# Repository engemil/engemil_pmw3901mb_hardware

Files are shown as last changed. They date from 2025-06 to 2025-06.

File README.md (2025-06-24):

# EngEmil PMW3901MB Optical Flow Sensor Module

The EngEmil PMW3901MB Module is a Optical Motion Tracking Chip module, for optical position control of drones. The PCB module is designed with KiCAD 9.

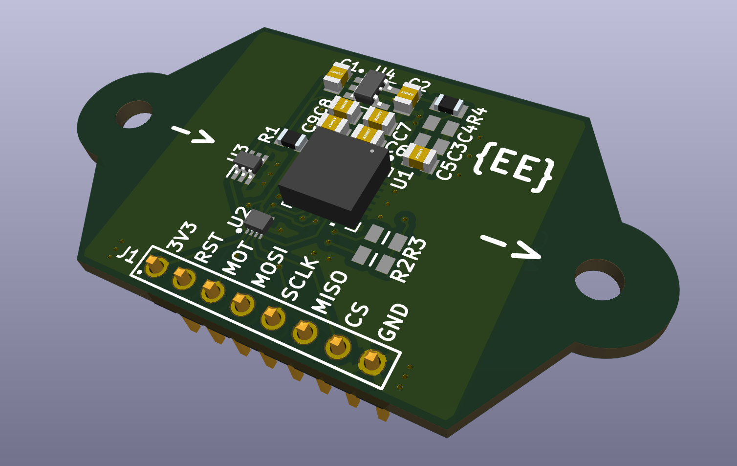
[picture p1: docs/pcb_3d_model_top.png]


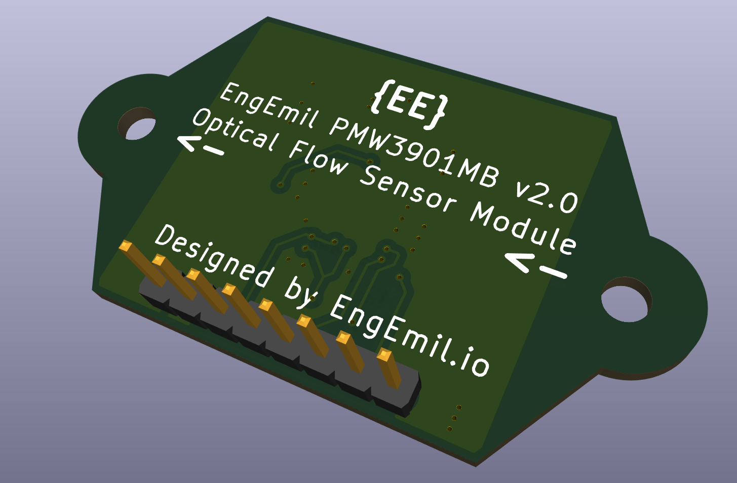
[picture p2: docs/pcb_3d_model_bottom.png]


## Versions

**Version 2**
- Removed 3v3 regulator and changed VCC pin text to 3V3
- Added ESD protection
- Added reverse voltage protection
- Added pull-up resistors for SCLK and MISO. Marked as not mounted.
- Added resistor for RC-filter for PMW3901MB. Marked as R4=0ohm, and C3 and C4 not mounted. Note added in schematic.

**Version 1**
- First prototype
- 3v3 regulator and 1v8 regulator
- Standard pins
- 2 mounting holes

## Links

- PMW3901MB-TXQT https://www.pixart.com/products-detail/44/PMW3901MB-TXQT
- Generating Gerbers (Manufacturer Recommendations): https://docs.oshpark.com/design-tools/kicad/generating-kicad-gerbers/
- Design Rule (Manufacturer Recommendations):
    - https://docs.oshpark.com/design-tools/kicad/kicad-design-rules/
    - https://www.pcbway.com/pcb_prototype/Pinted_Circuit_Board_Prototype.html
    - https://www.pcbway.com/capabilities.html
    - https://jlcpcb.com/capabilities/pcb-capabilities

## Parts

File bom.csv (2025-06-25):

Item # | Quantity | Manufacturer Part # | Description | Reference Designators | Not mount | Mounting Type | Package/Footprint | Manufacturer | Manufacturer Part Page | Note | Vendor #1 | Vendor #2 | Vendor #3
1 | 1 | TLV77318PDBVR | Fixed 1.8V voltage regulator | U4 |  | SMD | SOT-23-5 (DBV) | Texas Instrument | https://www.ti.com/product/TLV773/part-details/TLV77318PDBVR |  | https://www.digikey.no/no/products/detail/texas-instruments/tlv77318pdbvr/23331424 | https://no.mouser.com/ProductDetail/Texas-Instruments/TLV77318PDBVR?qs=i8QVZAFTkqTJuDP4u6TAYQ%3D%3D | https://lcsc.com/product-detail/Voltage-Regulators-Linear-Low-Drop-Out-LDO-Regulators_Texas-Instruments-TLV77318PDBVR_C32339535.html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
2 | 1 | 61300811121 | 2.54mm pitch 8 pins male through-hole headers | J1 |  | Through-hole |  | Würth Elektronik |  |  | https://www.digikey.no/en/products/detail/w%C3%BCrth-elektronik/61300811121/4846839
3 | 1 | PMW3901MB-TXQT | Optical Motion Tracing Chip | U1 |  | SMD | 28-pin QFN | Pixart | https://www.pixart.com/products-detail/44/PMW3901MB-TXQT |  | (Alibaba)
4 | 1 | RC0805FR-100RL | 0 Ohm 125mW resistor | R4 |  | SMD | 0805 in | YAGEO |  |  | https://no.mouser.com/ProductDetail/YAGEO/RC0805FR-100RL?qs=sGAEpiMZZMvdGkrng054t8AJgcdMkx7xHWXHpsqRQHI%3D
5 | 3 | RE0805FRE0710KL | 10k Ohm resistor | R1,R2,R3 | R2,R3 | SMD | 0805 in | YAGEO |  |  | https://no.mouser.com/ProductDetail/YAGEO/RE0805FRE0710KL
6 | 2 | C0805C226M9PAC7210 | 22uF ceramic non-polarity capacitor | C3,C4 | C3,C4 | SMD | 0805 in | YAGEO KEMET |  |  | https://no.mouser.com/ProductDetail/KEMET/C0805C226M9PAC7210?qs=kSrfU%2F8XGbk4aYGfk4dTXw%3D%3D
7 | 3 | C0805C104JMRECAUTO7210 | 100n/0.1uF ceramic non-polarity capacitor | C5,C6,C8 |  | SMD | 0805 in | YAGEO KEMET |  |  | https://no.mouser.com/ProductDetail/KEMET/C0805C104JMRECAUTO7210?qs=55YtniHzbhCWsM9aesOnTg%3D%3D
8 | 2 | C0805C105J4RECAUTO7210 | 1uF 16VDC 5% ceramic non-polarity capacitor | C1,C2 |  | SMD | 0805 in | YAGEO KEMET |  |  | https://no.mouser.com/ProductDetail/KEMET/C0805C105J4RECAUTO7210?qs=55YtniHzbhDbyzfJO59W6Q%3D%3D#
9 | 1 | C0805C106K4PAC7210 | 10uF ceramic non-polarity capacitor | C7 |  | SMD | 0805 in | YAGEO KEMET |  |  | https://no.mouser.com/ProductDetail/KEMET/C0805C106K4PAC7210?qs=zDkSFN9STR9jrJZBgSwCDA%3D%3D
10 | 1 | C0805C475K4RACAUTO7210 | 4.7uF ceramic non-polarity capacitor | C9 |  | SMD | 0805 in | YAGEO KEMET |  |  | https://no.mouser.com/ProductDetail/KEMET/C0805C475K4RACAUTO7210?qs=HXFqYaX1Q2xkgxFv524wgg%3D%3D
11 | 1 | TPD8E003DQDR | TVS diodes package | U2 |  | SMD |  | Texas Instrument |  |  | https://no.mouser.com/ProductDetail/Texas-Instruments/TPD8E003DQDR?qs=hEBn5lgDlCo1%252BvgoUxxo%252Bg%3D%3D
12 | 1 | LM66100QDCKRQ1 | Reverse polarity protection | U3 |  | SMD | SC70-6 | Texas Instrument | https://www.ti.com/product/LM66100-Q1 |  | https://no.mouser.com/ProductDetail/Texas-Instruments/LM66100QDCKRQ1?qs=MyNHzdoqoQIvjdvtKQd0jA%3D%3D

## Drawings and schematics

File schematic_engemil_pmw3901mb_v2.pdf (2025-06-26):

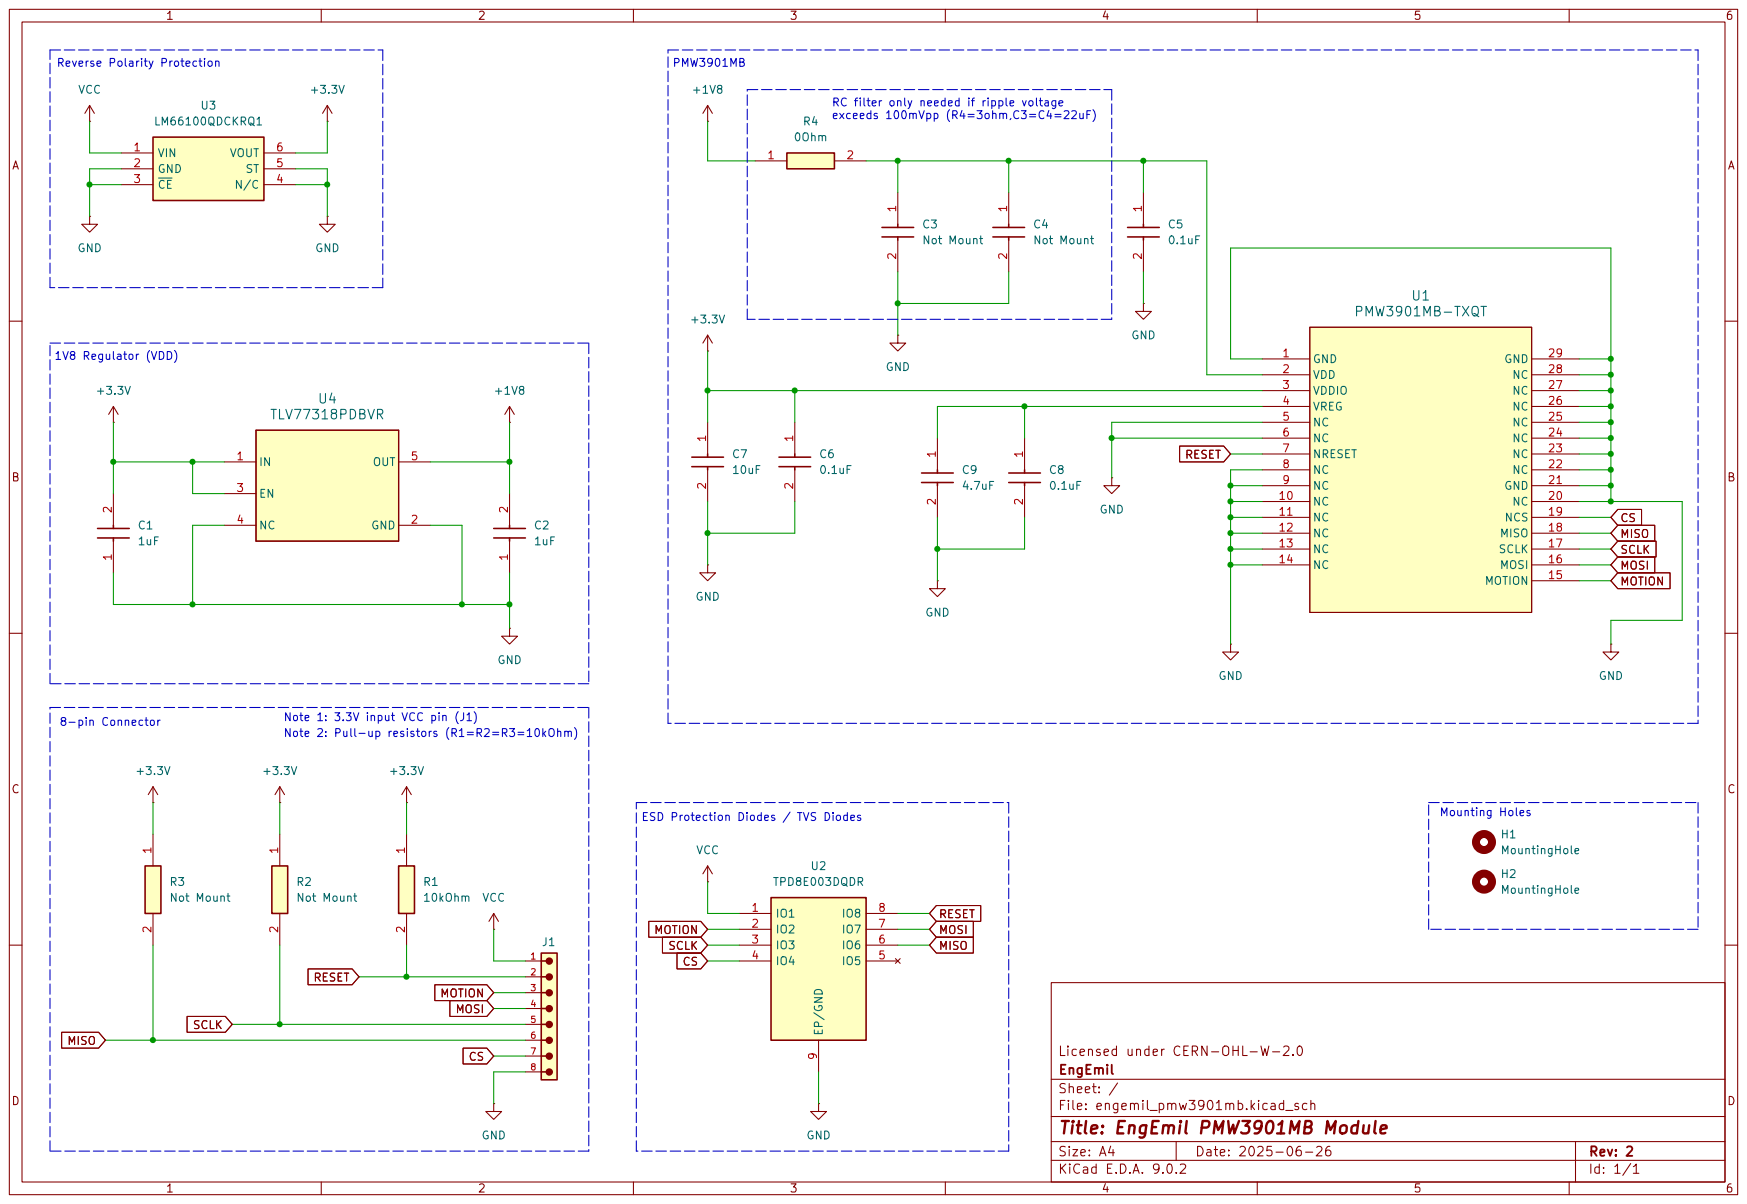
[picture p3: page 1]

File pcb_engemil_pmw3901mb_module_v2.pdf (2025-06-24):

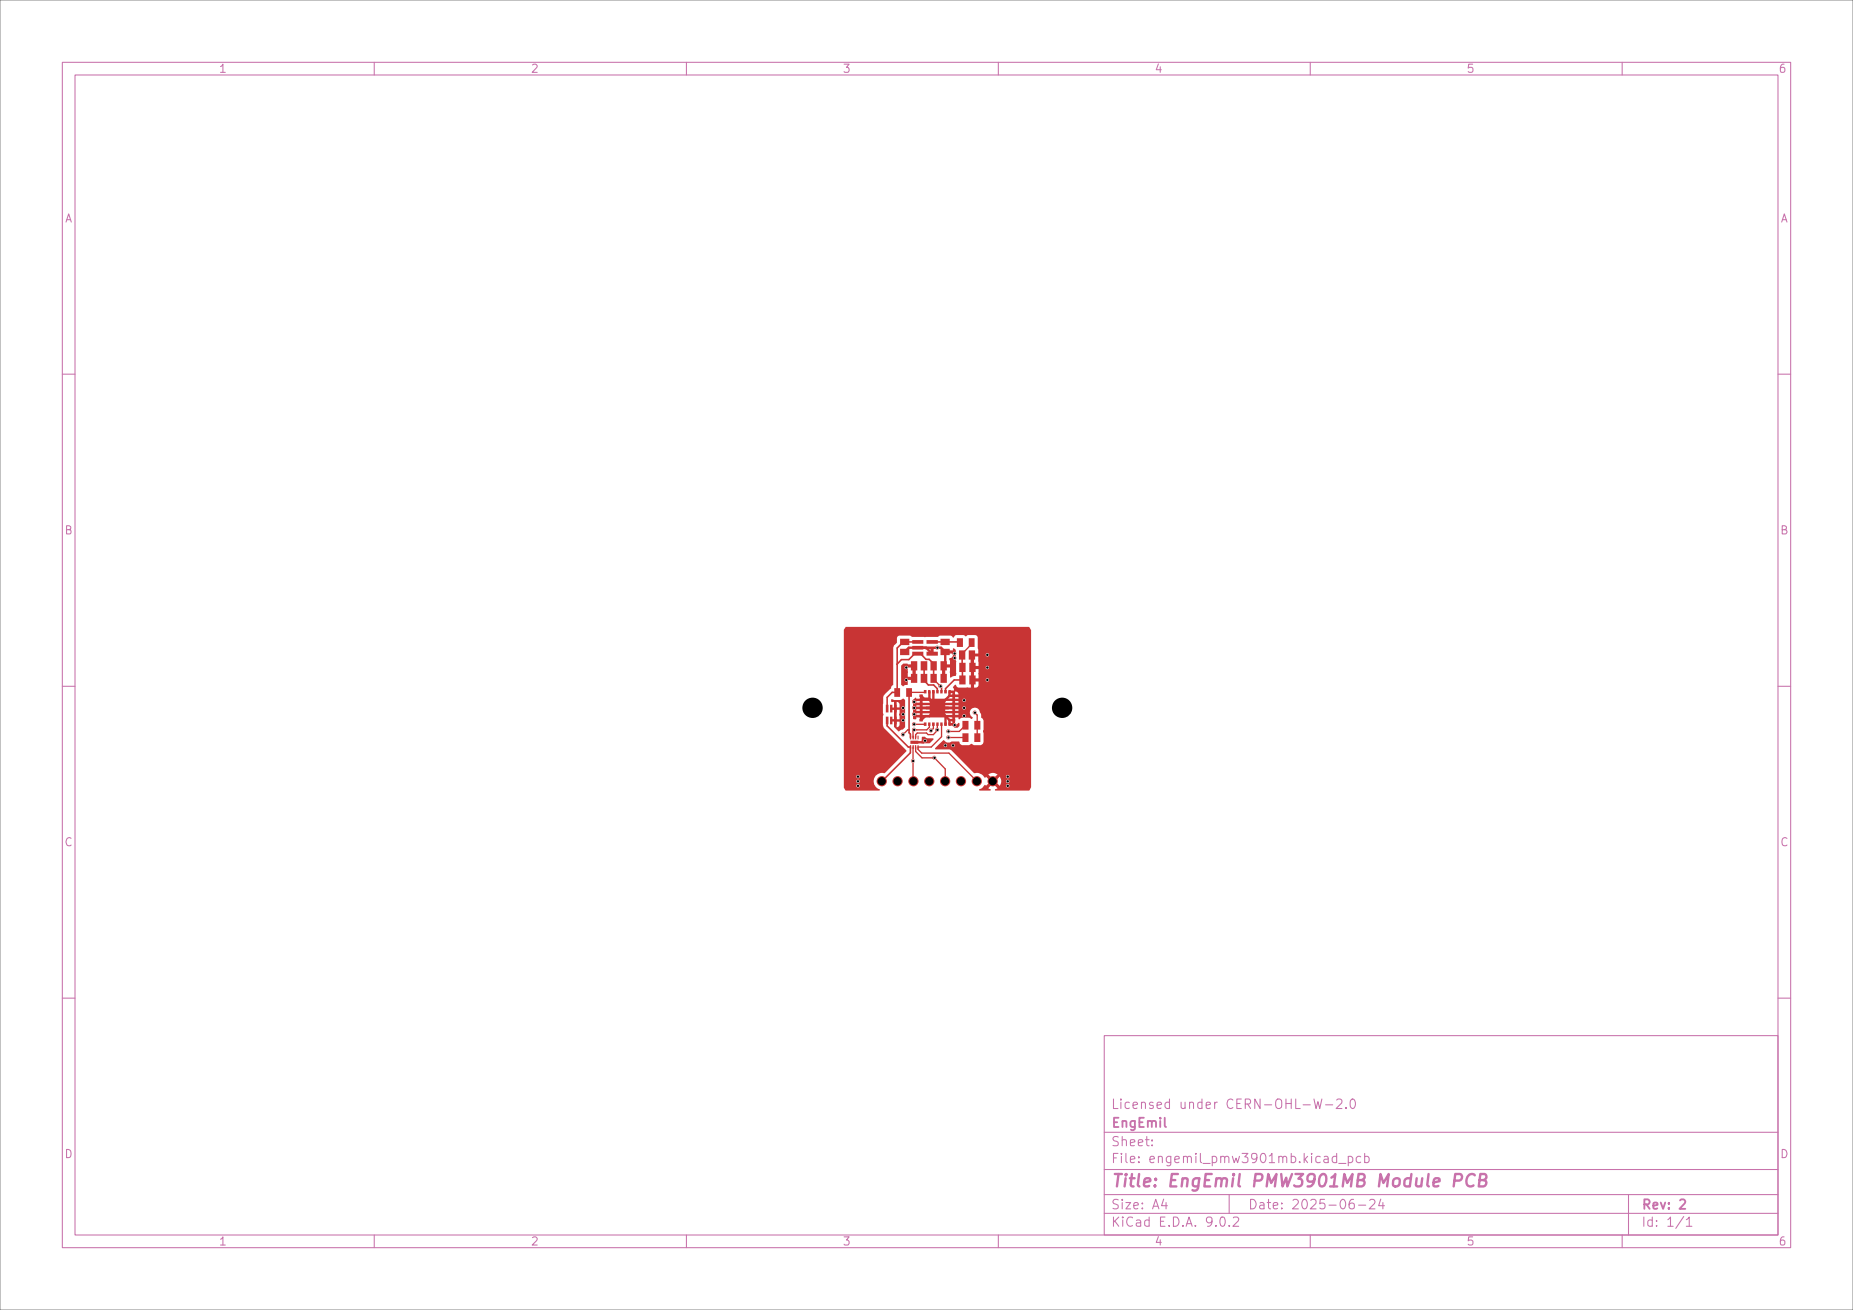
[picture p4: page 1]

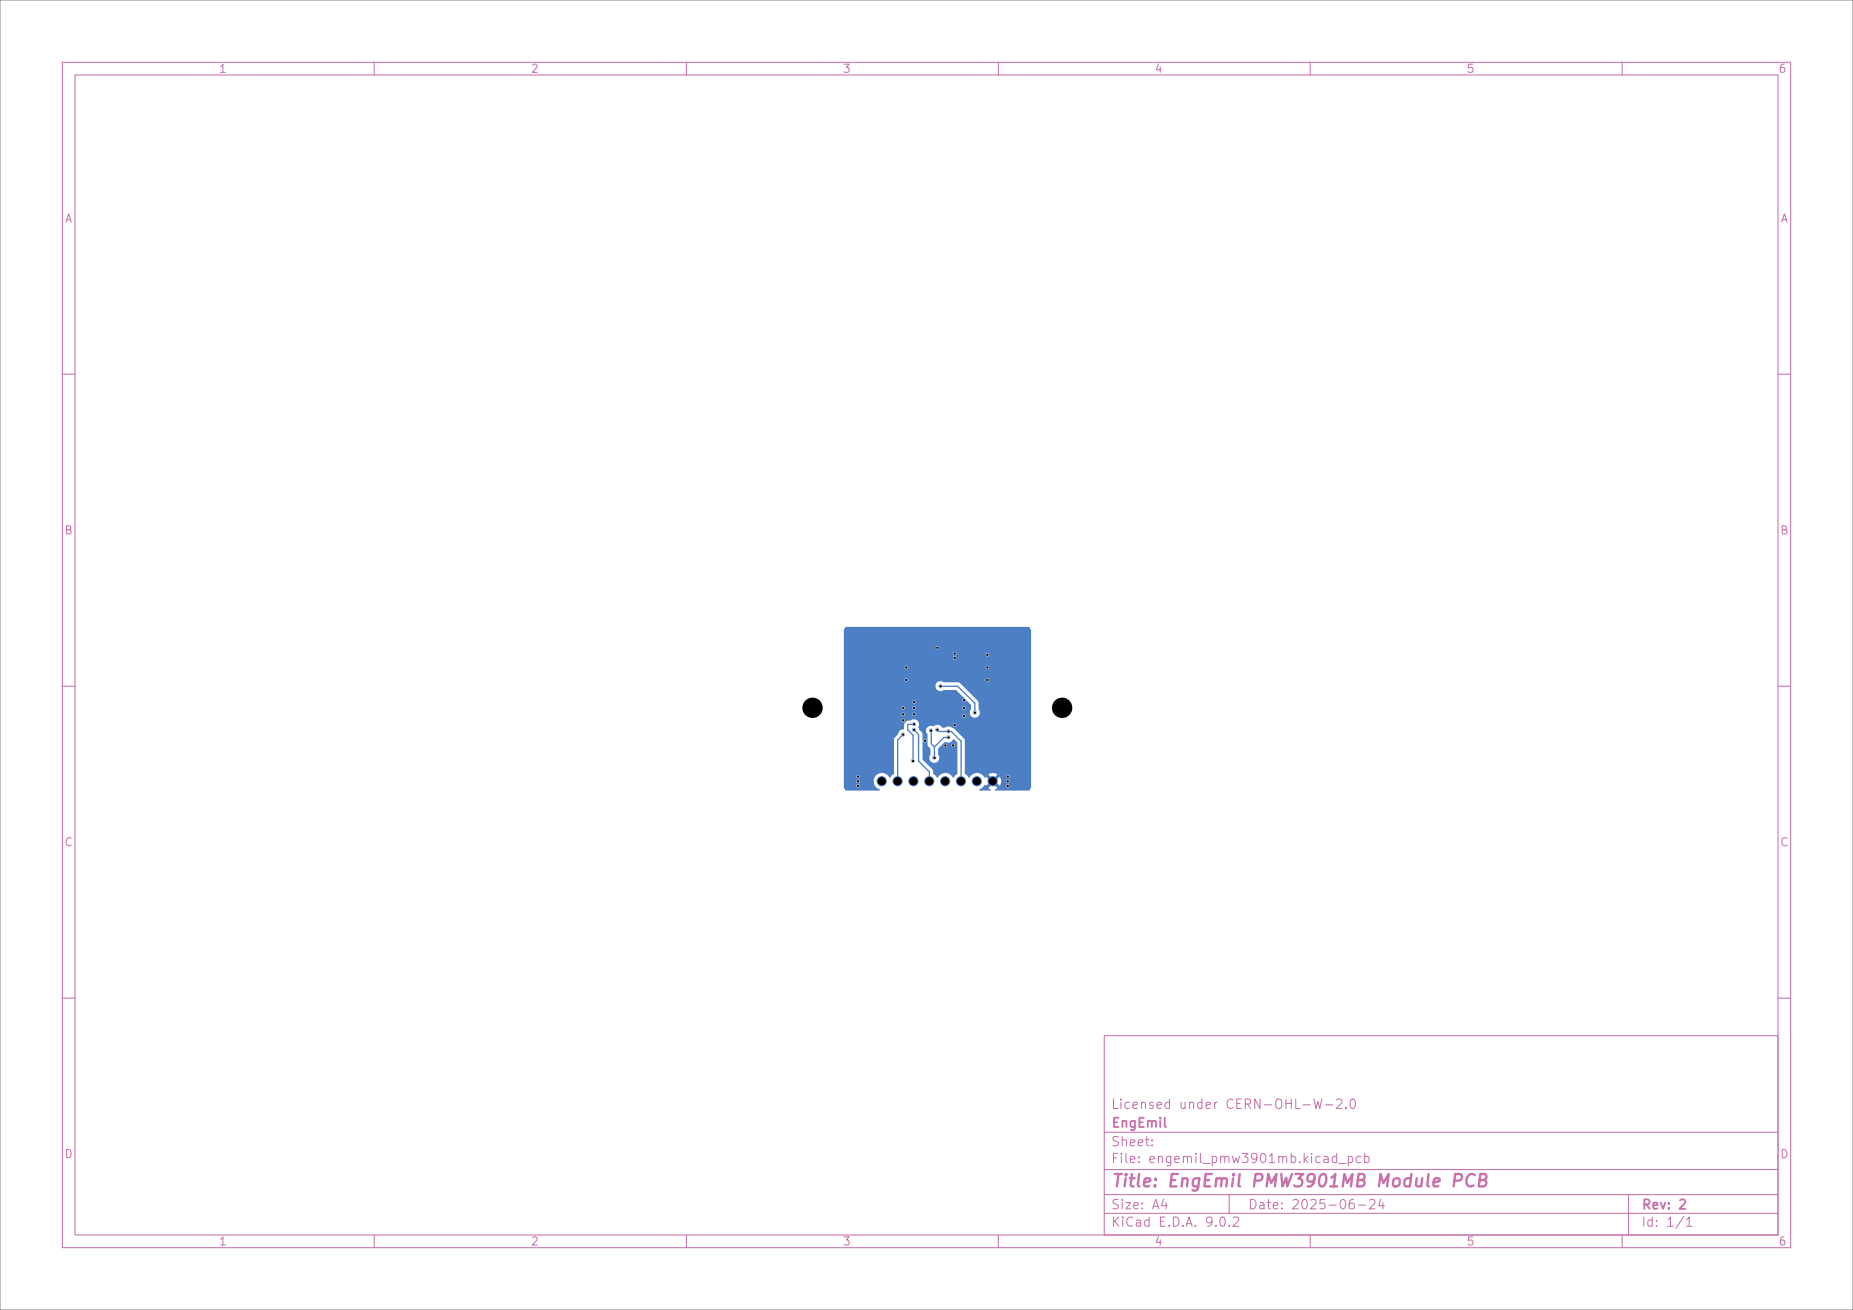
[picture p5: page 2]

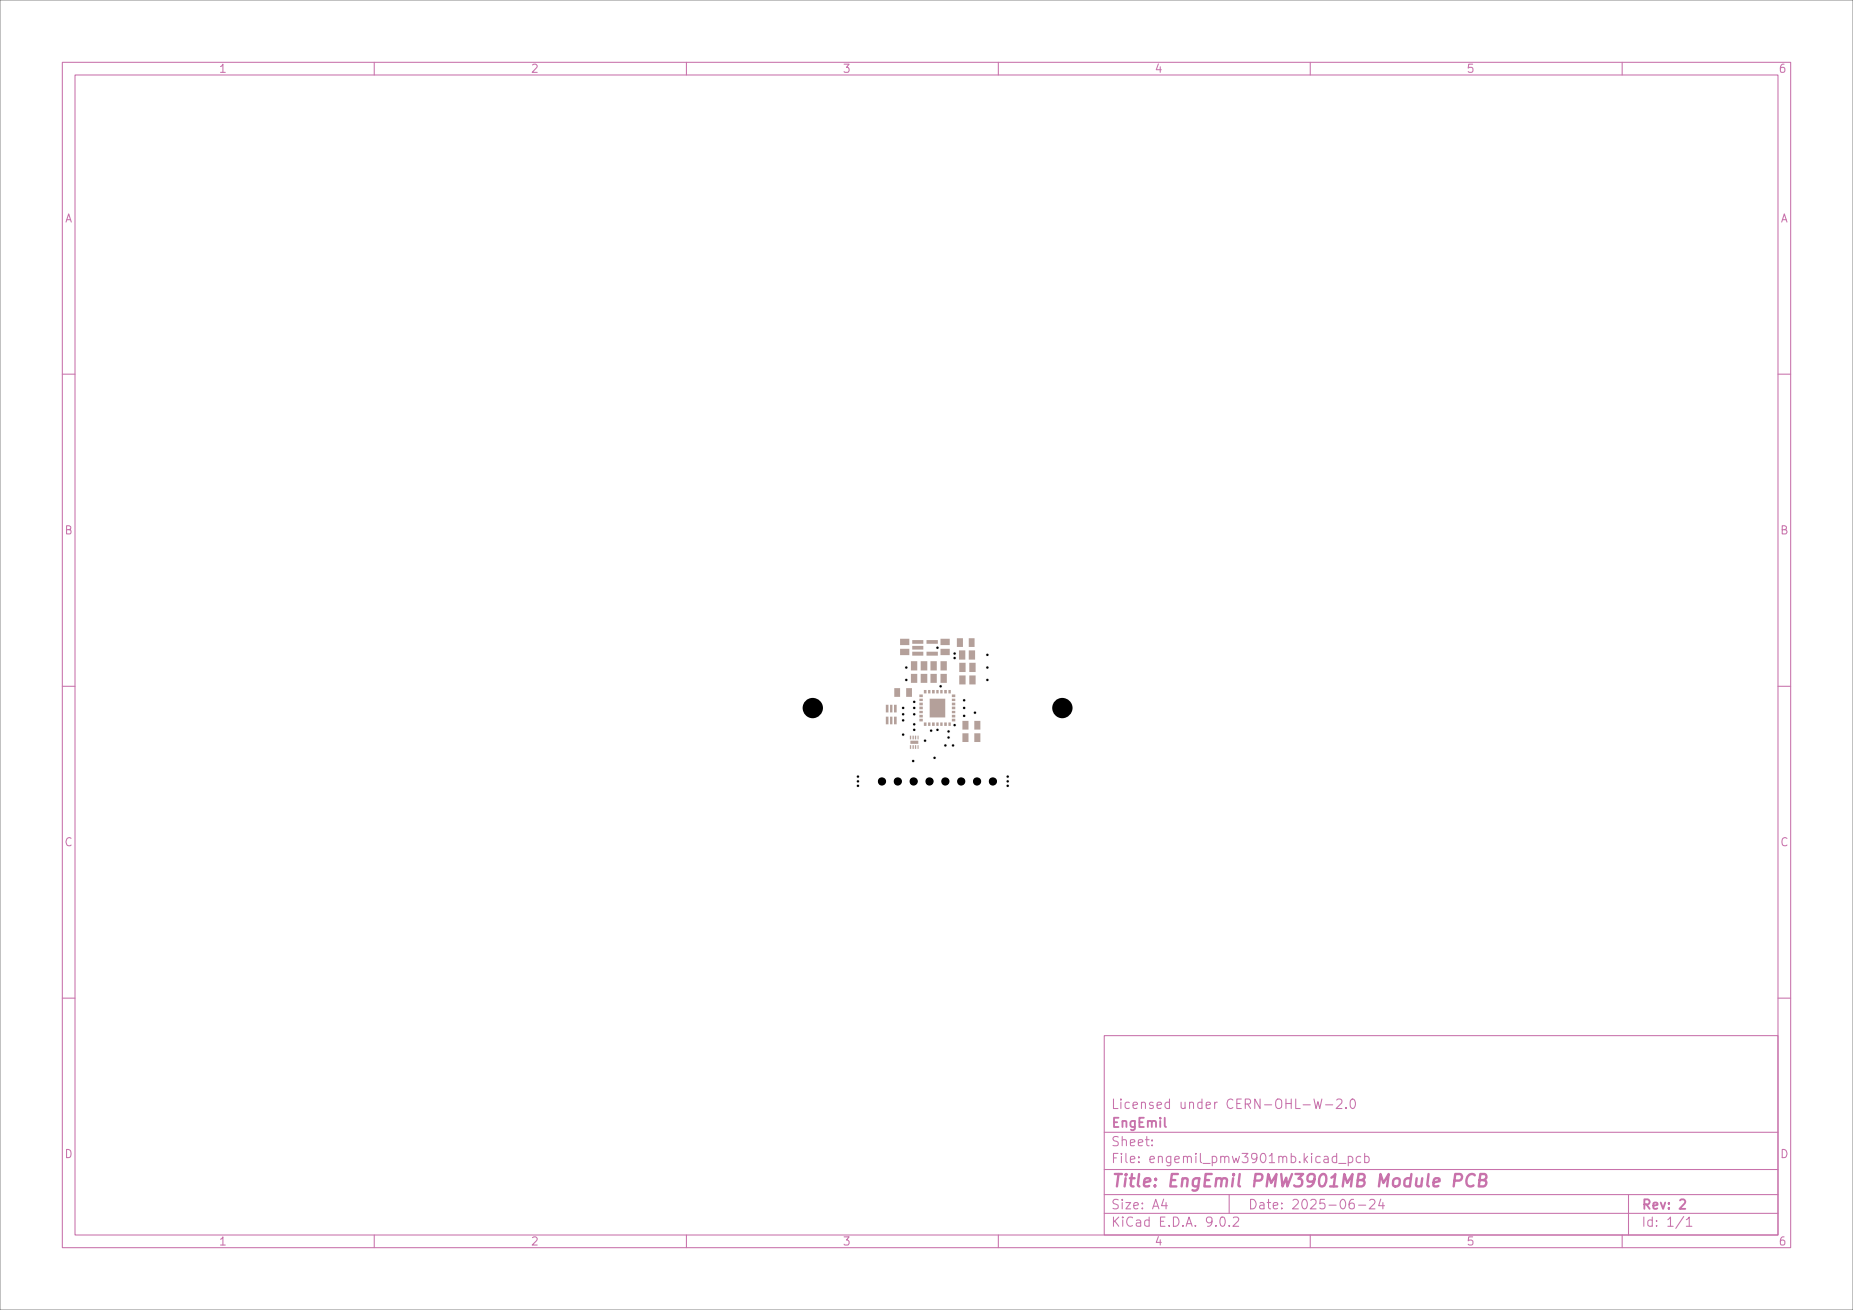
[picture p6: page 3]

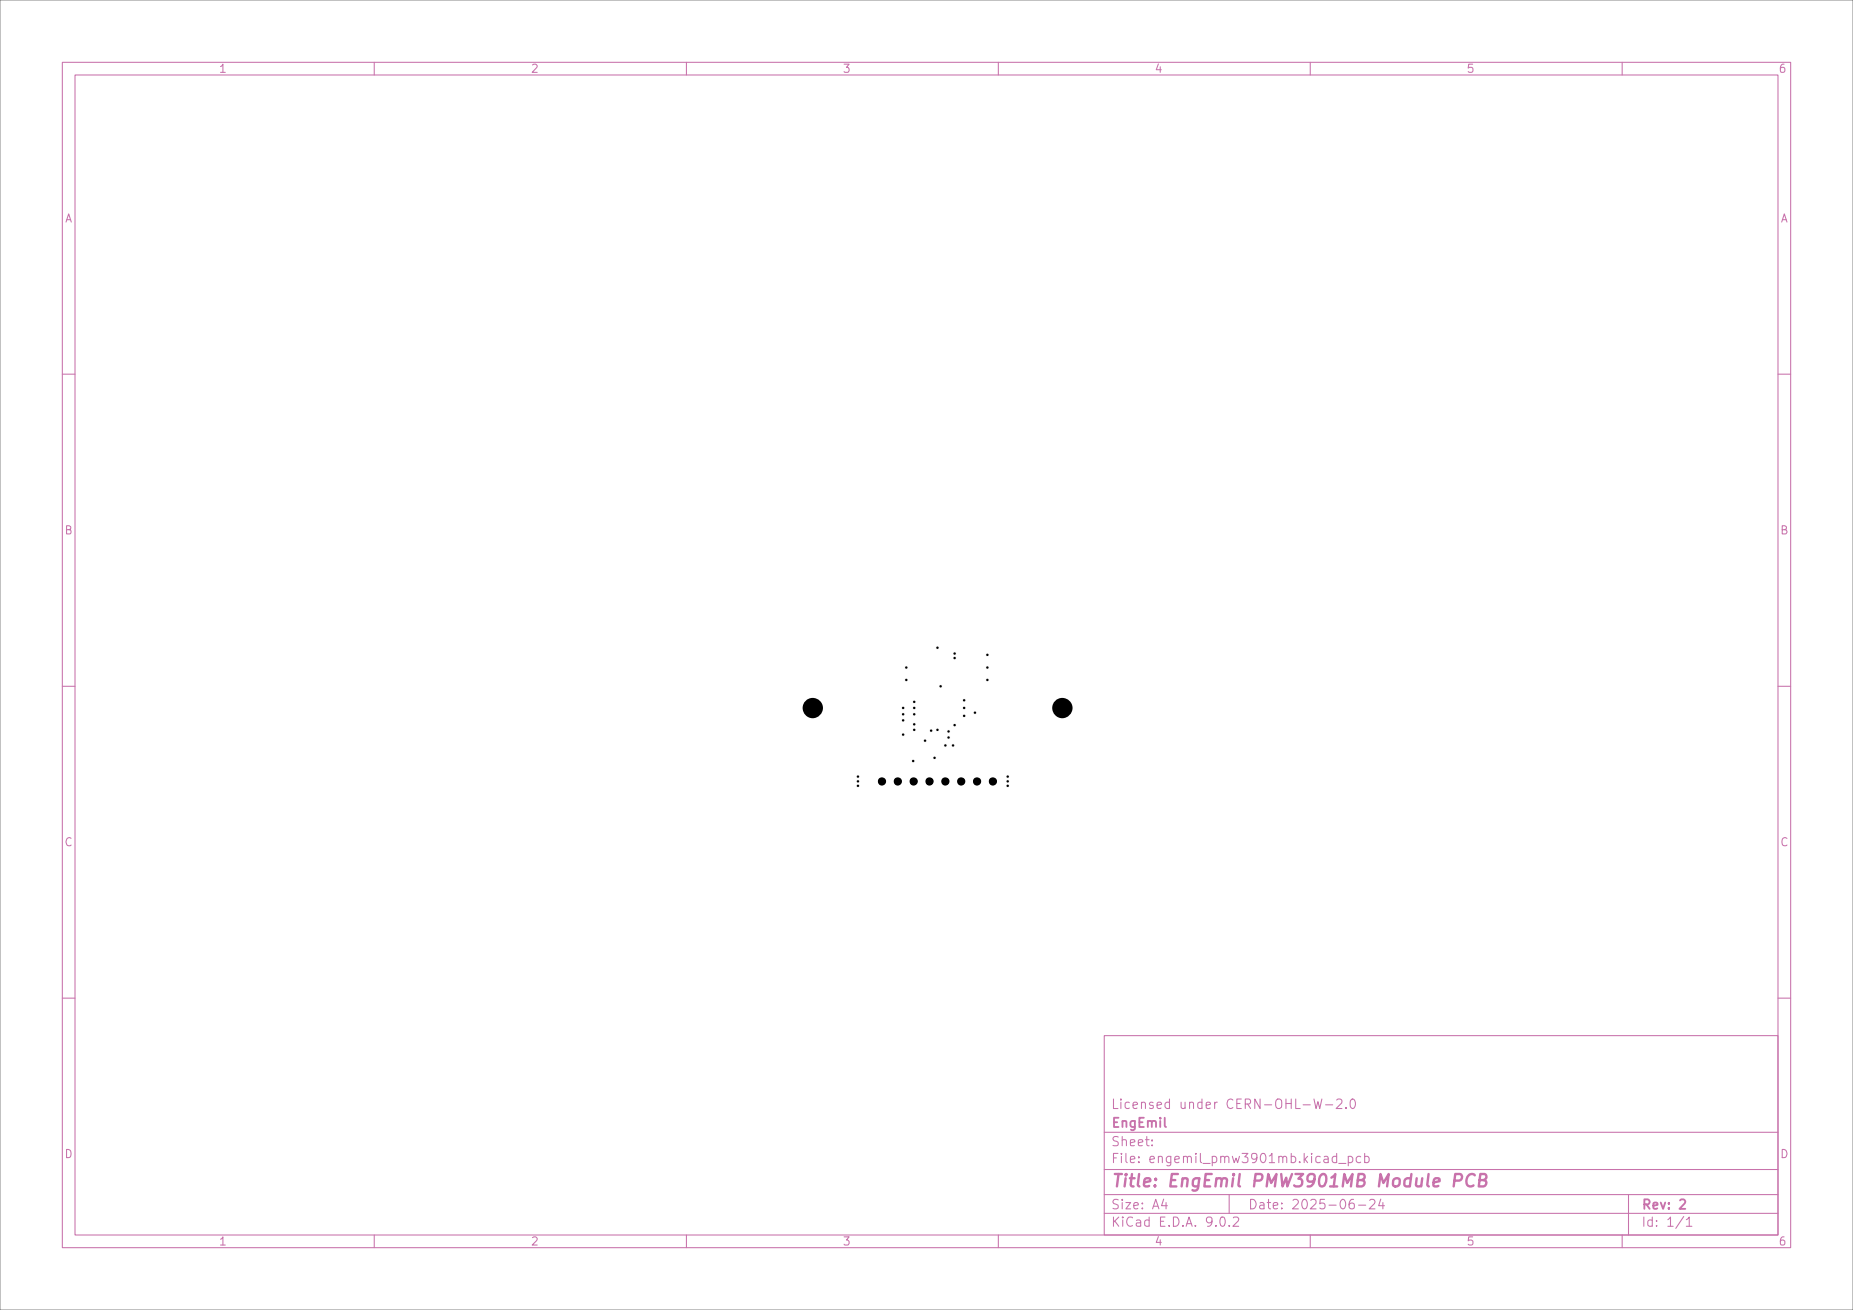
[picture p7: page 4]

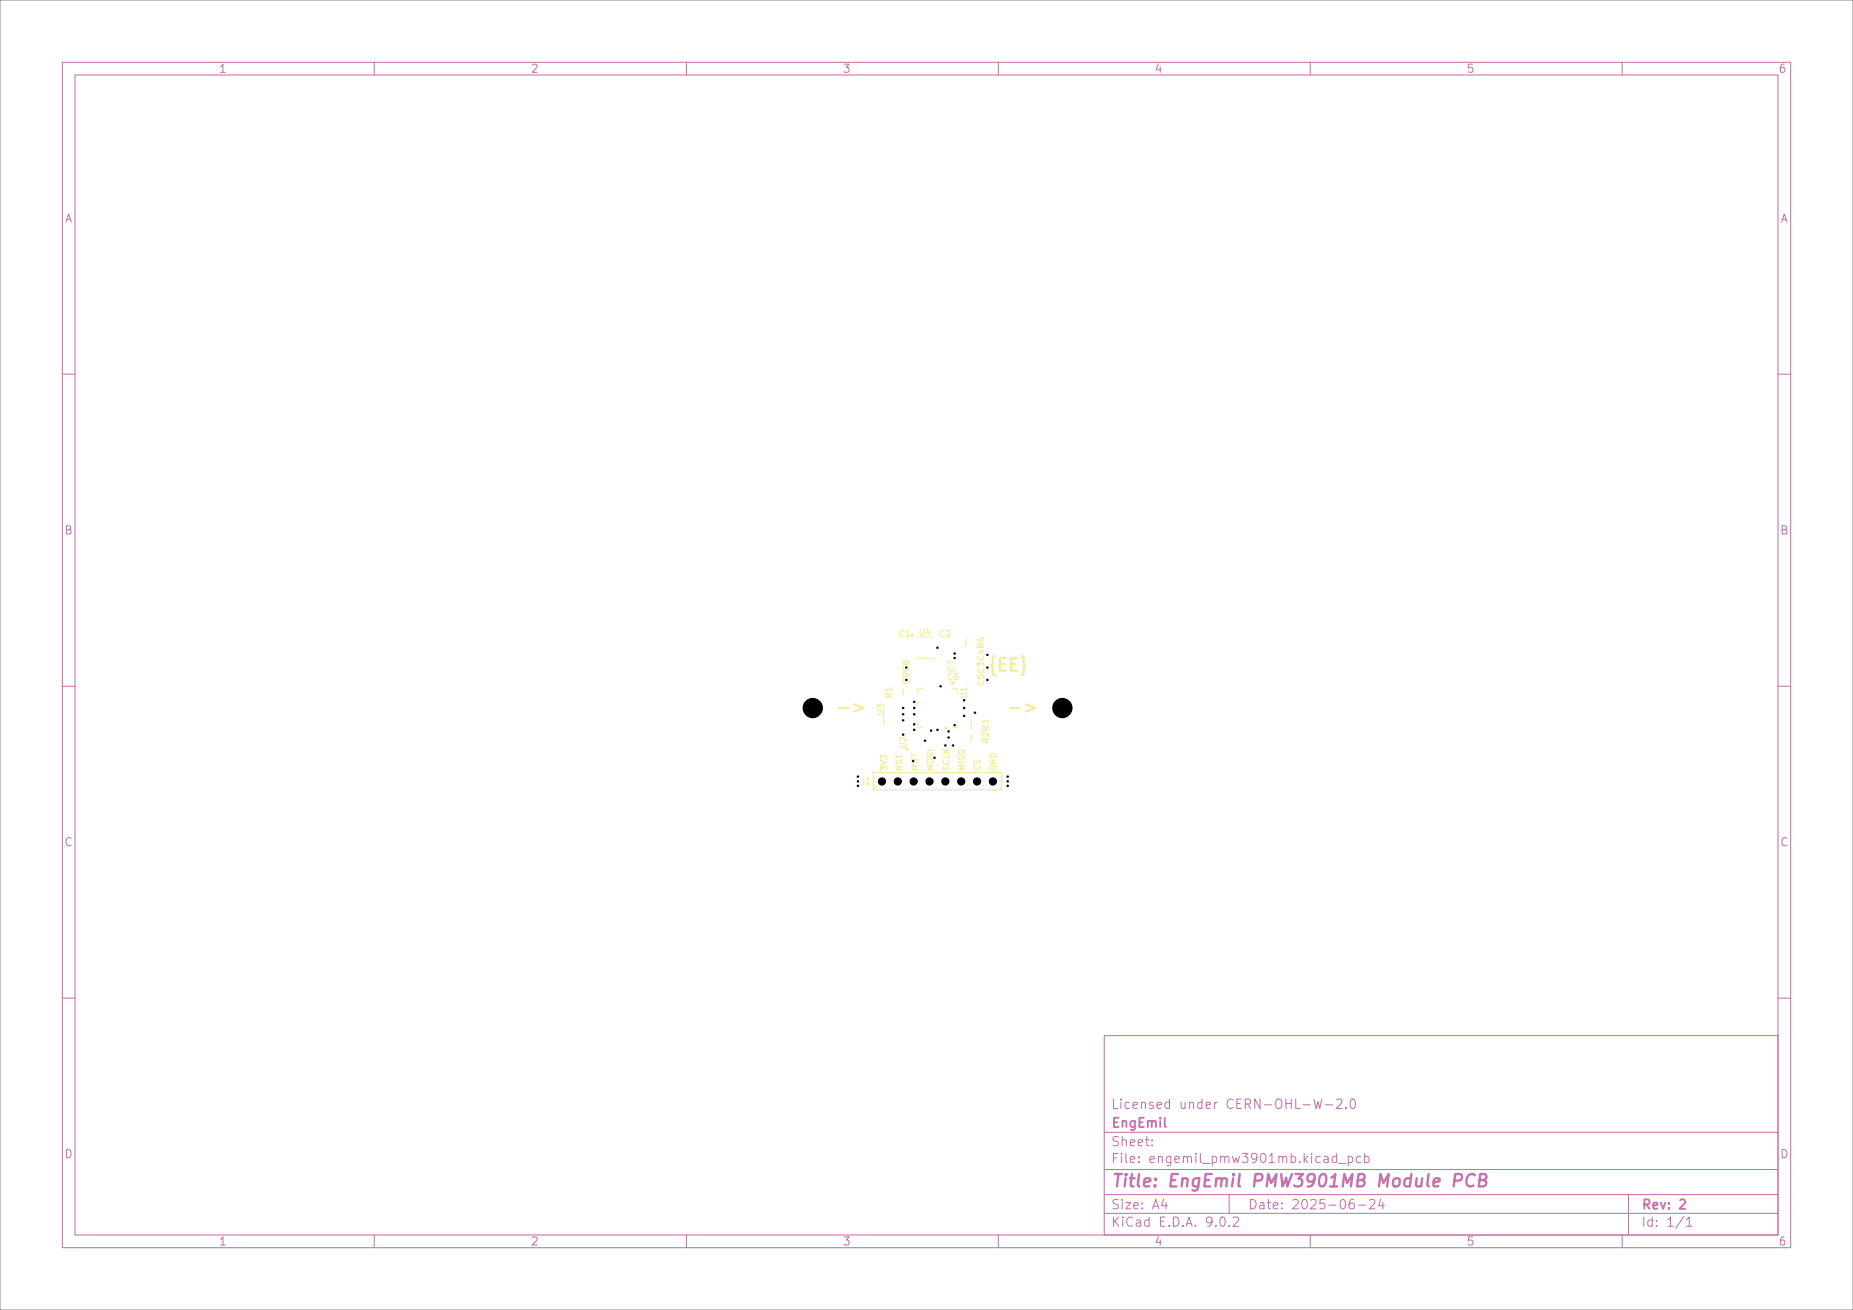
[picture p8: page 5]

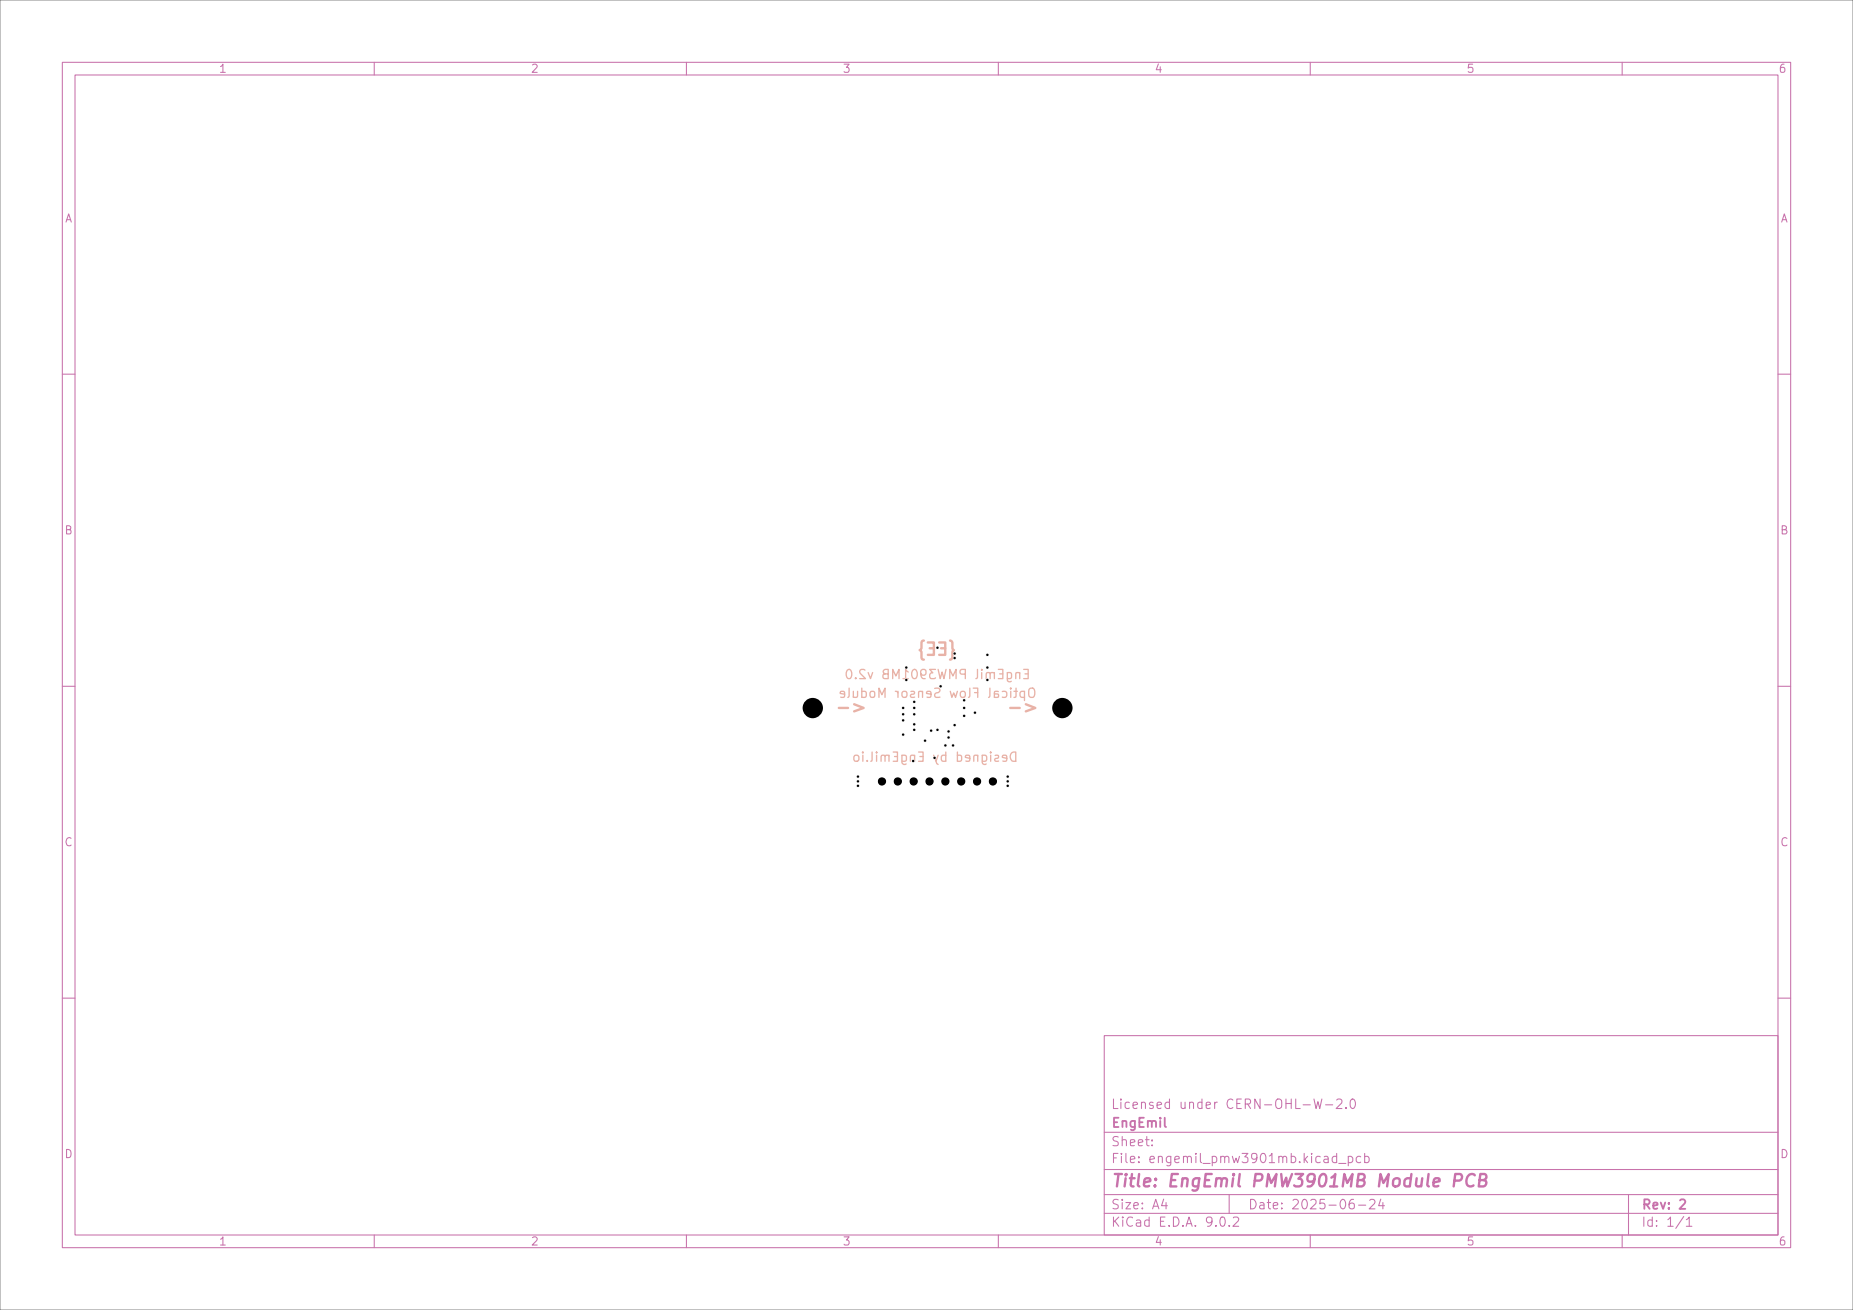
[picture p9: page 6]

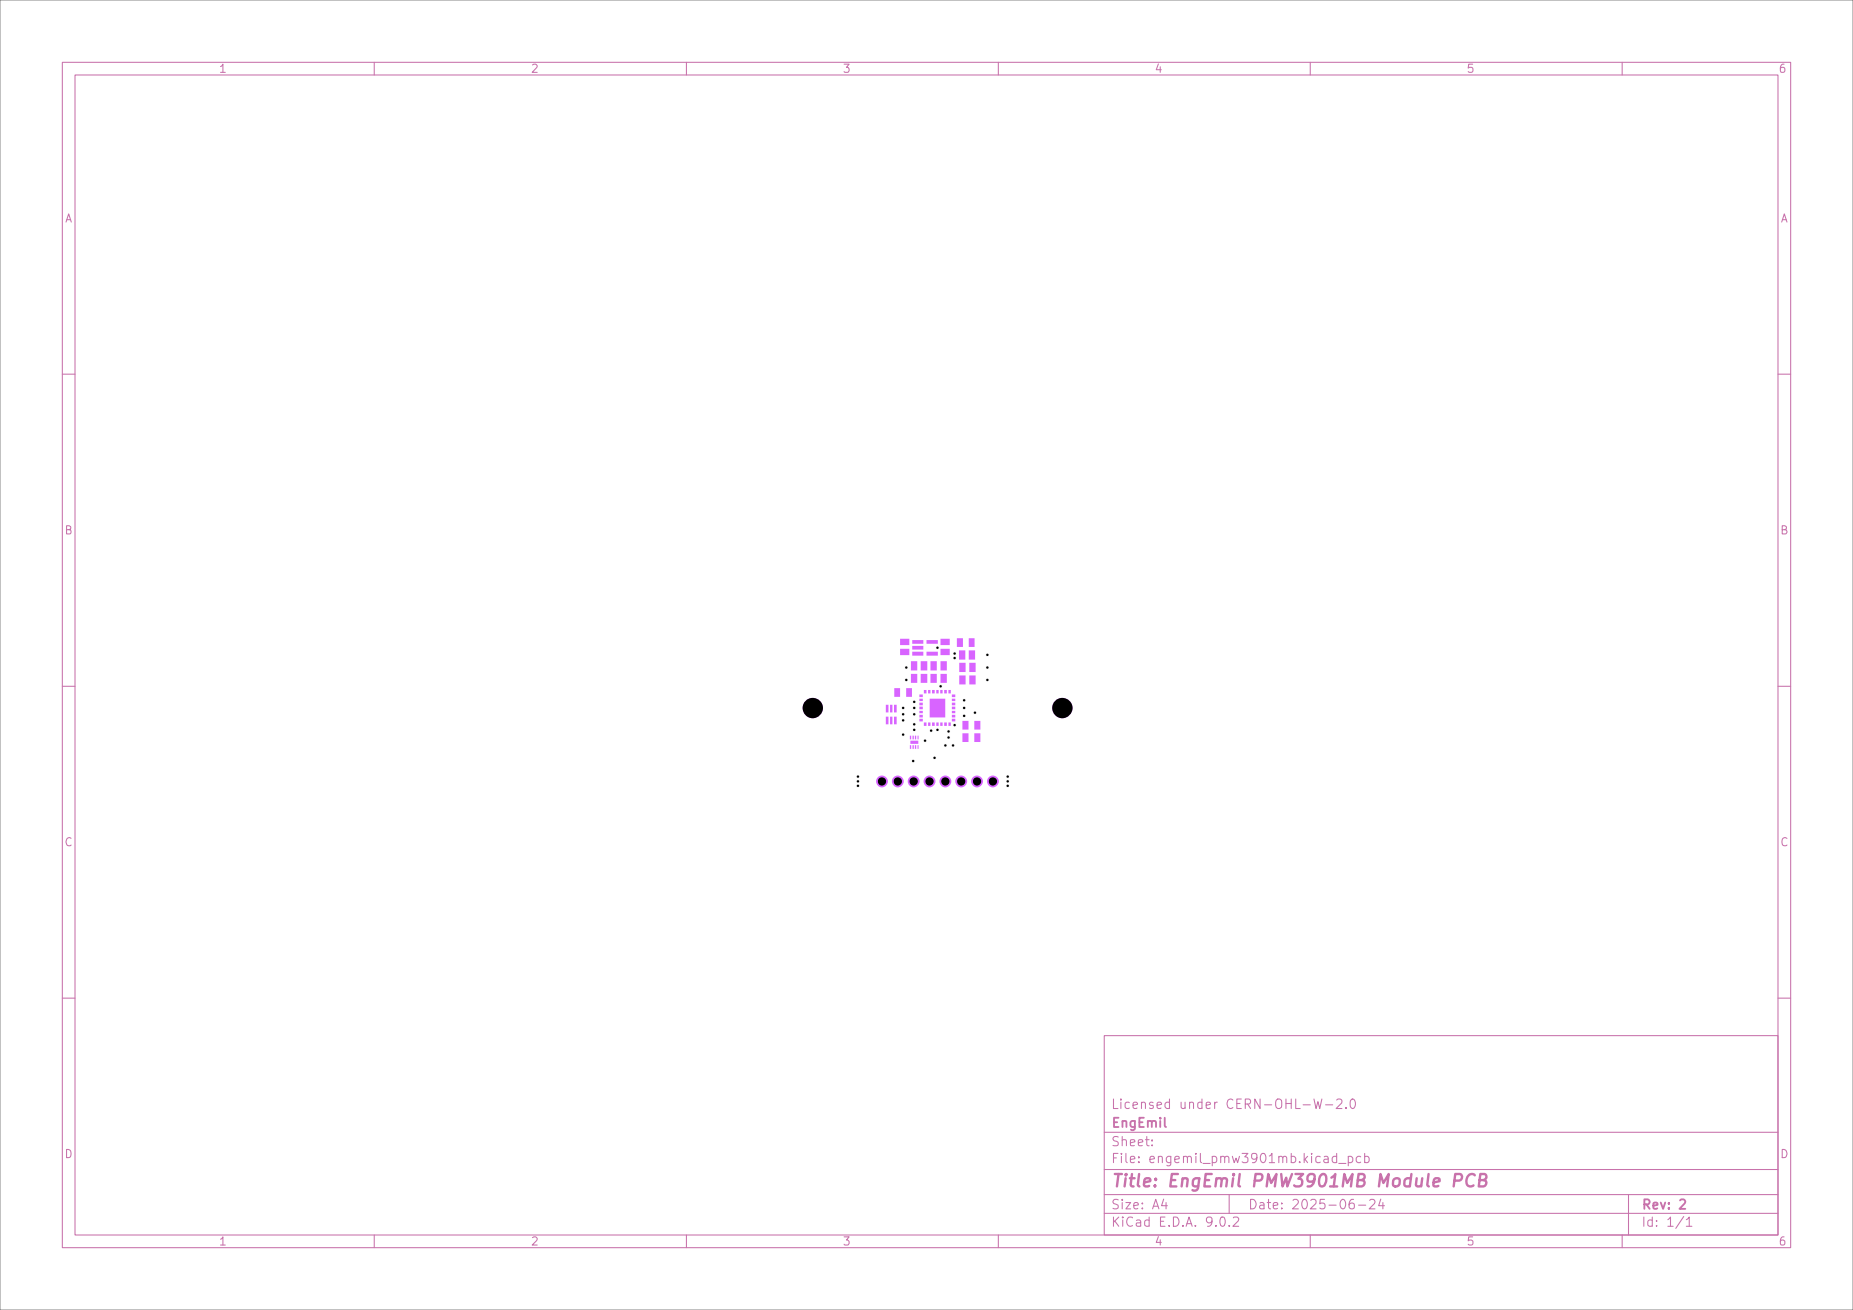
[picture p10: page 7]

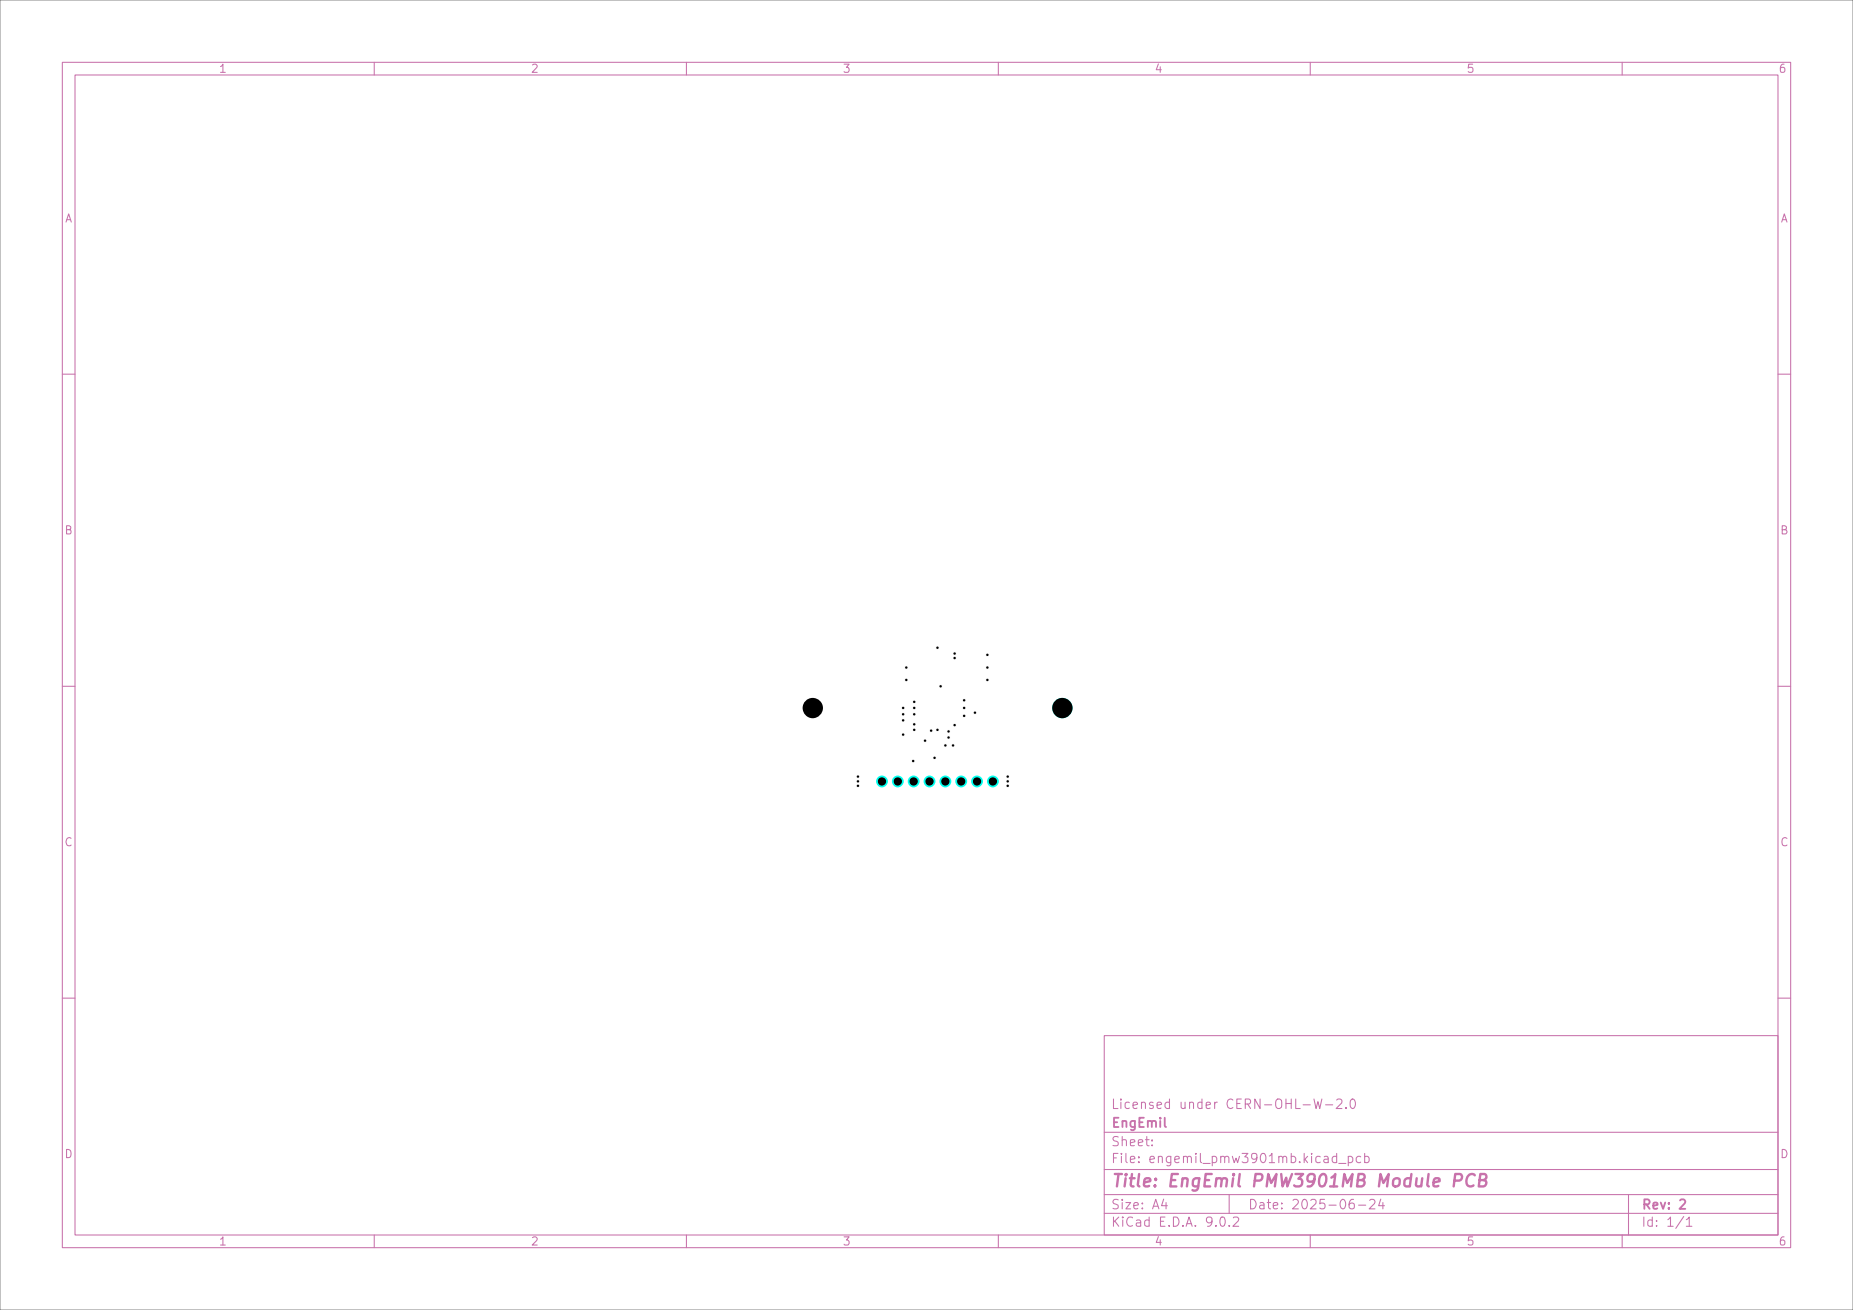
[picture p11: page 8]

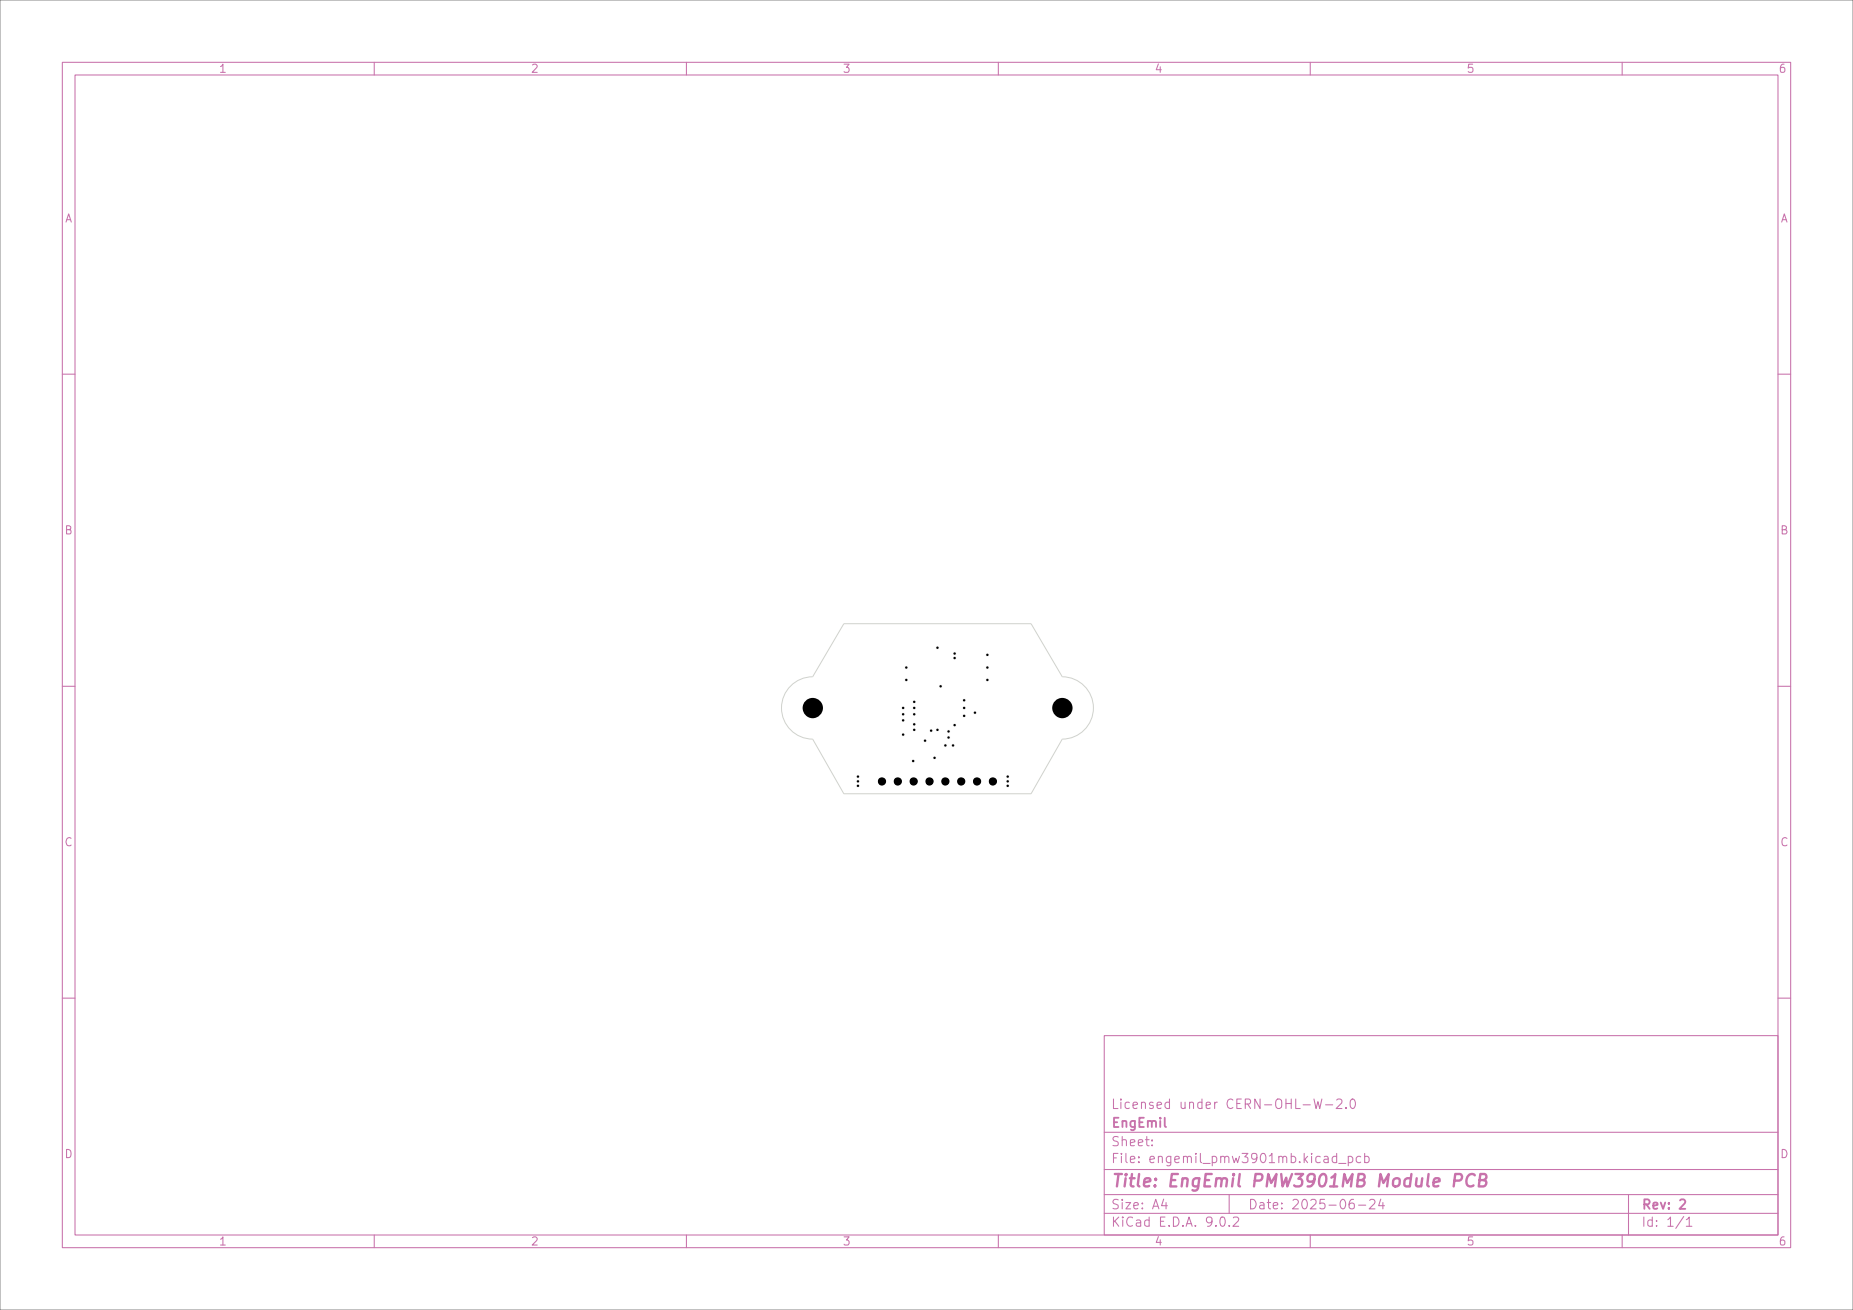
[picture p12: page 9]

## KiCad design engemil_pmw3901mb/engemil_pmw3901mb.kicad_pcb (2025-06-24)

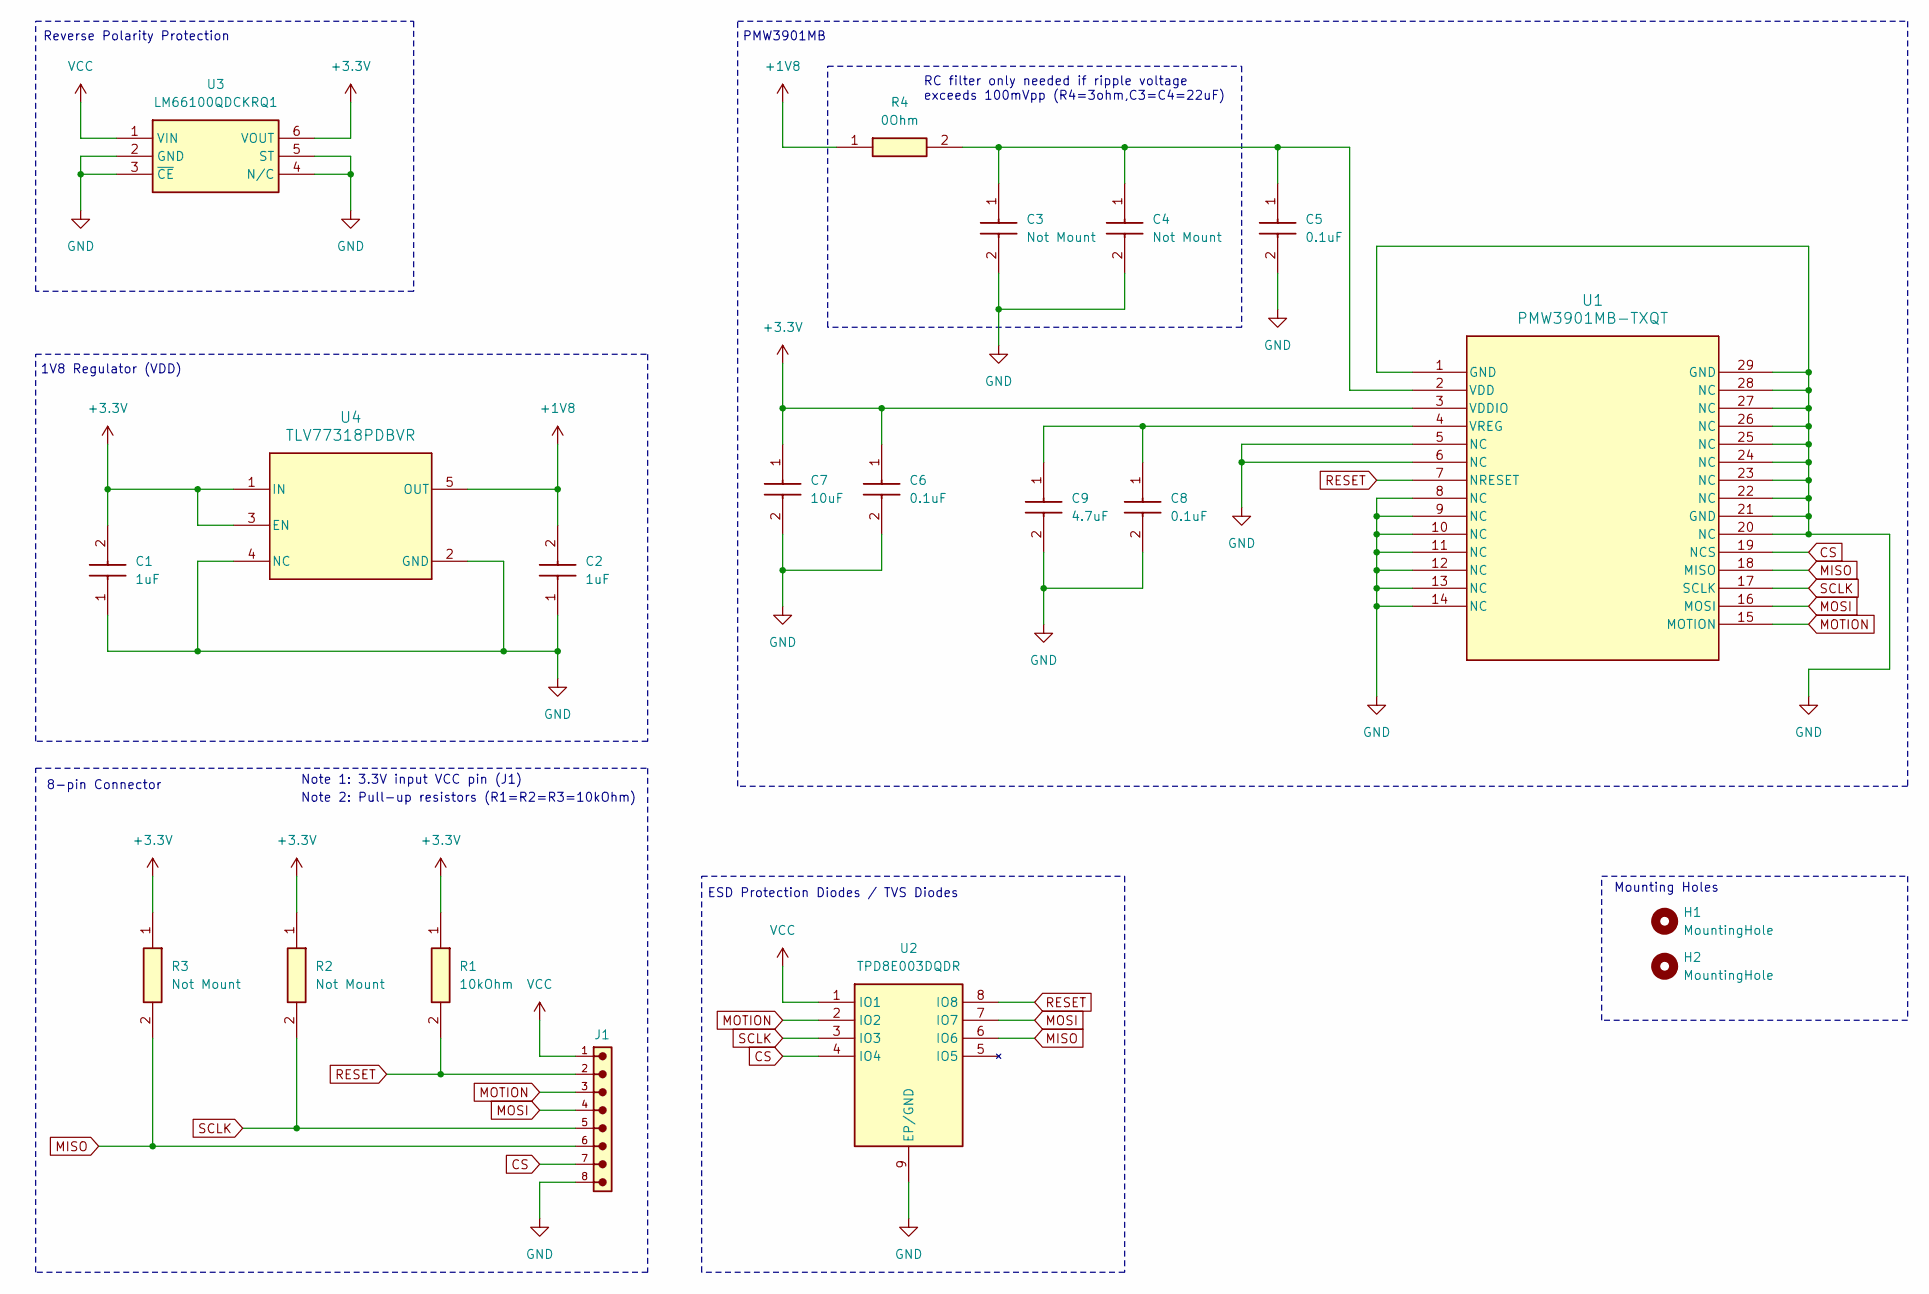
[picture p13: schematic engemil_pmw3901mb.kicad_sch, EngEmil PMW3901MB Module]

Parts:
C1, C2: 1uF; CAPC2012X110N; Mouser Part Number 80-C0805C105J4REAULR
C3, C4: Not Mount; CAPC2012X110N; Mouser Part Number 80-C0805C226M9PACLR
C5, C6, C8: 0.1uF; CAPC2012X110N; Mouser Part Number 80-C0805C104JMREAULR
C7: 10uF; CAPC2012X110N; Mouser Part Number 80-C0805C106K4P7210
C9: 4.7uF; CAPC2012X110N; Mouser Part Number 80-C0805C475K4RAUTLR
H1, H2: MountingHole; MountingHole_3.2mm_M3_ISO14580
J1: 6130XX11121; 61300811121
R1: 10kOhm; RESC2012X60N; Mouser Part Number 603-RE0805FRE0710KL
R2, R3: Not Mount; RESC2012X60N; Mouser Part Number 603-RE0805FRE0710KL
R4: 0Ohm; RESC2012X60N; Mouser Part Number 603-RC0805FR-100RL
U1: PMW3901MB-TXQT; QFN_01MB-TXQT_PIX
U2: TPD8E003DQDR; SON40P135X170X80-9N; Mouser Part Number 595-TPD8E003DQDR
U3: LM66100QDCKRQ1; SOT65P210X110-6N; Mouser Part Number 595-LM66100QDCKRQ1
U4: TLV77318PDBVR; DBV0005A-IPC_A

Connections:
+1V8: C2.2, R4.1, U4.5 (OUT)
+3.3V: C1.2, C6.1, C7.1, R1.1, R2.1, R3.1, U1.3 (VDDIO), U3.6 (VOUT), U4.1 (IN), U4.3 (EN)
CS: J1.7, U1.19 (NCS), U2.4 (IO4)
GND: C1.1, C2.1, C3.2, C4.2, C5.2, C6.2, C7.2, C8.2, C9.2, J1.8, U1.1 (GND), U1.5 (NC), U1.6 (NC), U1.8 (NC), U1.9 (NC), U1.10 (NC), U1.11 (NC), U1.12 (NC), U1.13 (NC), U1.14 (NC), U1.20 (NC), U1.21 (GND), U1.22 (NC), U1.23 (NC), U1.24 (NC), U1.25 (NC), U1.26 (NC), U1.27 (NC), U1.28 (NC), U1.29 (GND), U2.9 (EP/GND), U3.2 (GND), U3.3 (~CE), U3.4 (N/C), U3.5 (ST), U4.2 (GND), U4.4 (NC)
MISO: J1.6, R3.2, U1.18 (MISO), U2.6 (IO6)
MOSI: J1.4, U1.16 (MOSI), U2.7 (IO7)
MOTION: J1.3, U1.15 (MOTION), U2.2 (IO2)
unnamed: C3.1, C4.1, C5.1, R4.2, U1.2 (VDD)
unnamed: C8.1, C9.1, U1.4 (VREG)
RESET: J1.2, R1.2, U1.7 (NRESET), U2.8 (IO8)
SCLK: J1.5, R2.2, U1.17 (SCLK), U2.3 (IO3)
VCC: J1.1, U2.1 (IO1), U3.1 (VIN)

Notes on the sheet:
Mounting Holes
8-pin Connector
ESD Protection Diodes / TVS Diodes
Note 1: 3.3V input VCC pin (J1)
PMW3901MB
Reverse Polarity Protection
Note 2: Pull-up resistors (R1=R2=R3=10kOhm)
RC filter only needed if ripple voltage exceeds 100mVpp (R4=3ohm,C3=C4=22uF)
1V8 Regulator (VDD)

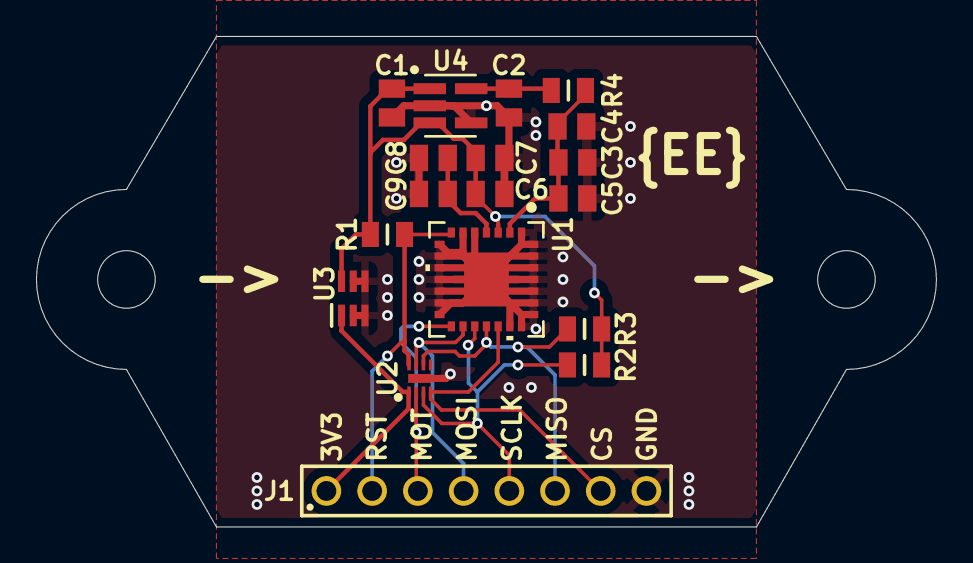
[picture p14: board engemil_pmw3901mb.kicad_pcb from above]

Board: 2 copper layers, 50.0 x 27.2 mm, 20 parts (0 on the bottom side), 12 nets.

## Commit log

2025-06-06 Added license and base kicad project
    [engemil_pmw3901mb.kicad_pcb, engemil_pmw3901mb.kicad_sch]
2025-06-08 Added docs folder with datasheet, added info in title block of schematic, added info in readme
    [engemil_pmw3901mb.kicad_sch]
2025-06-09 - Added BOM file - Added datasheets under docs folder - Added symbol, footprint and 3d models to lib - Added readme files to subfolder of lib - Added raw folder for lib - Designed voltage regulators 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
    [bom.csv, engemil_pmw3901mb.kicad_sch]
2025-06-10 Updated bom and raw files
    [bom.csv]
2025-06-10 - Added more components to the BOM - Added component EDA/CAD files to the lib folder - Finished first version of Schematic
    [bom.csv, engemil_pmw3901mb.kicad_sch]
2025-06-11 - Updated Schematic date - First orientation of components in pcb editor
    [engemil_pmw3901mb.kicad_pcb, engemil_pmw3901mb.kicad_sch]
2025-06-11 - Updated notes in schematic - Updated PMW3901MB NCS pin fron not connected to unspecified - Updated component orientation in PCB editor
    [engemil_pmw3901mb.kicad_pcb, engemil_pmw3901mb.kicad_sch]
2025-06-11 Updated schematic and pcb
    [engemil_pmw3901mb.kicad_pcb, engemil_pmw3901mb.kicad_sch]
2025-06-12 - Added mounting holes in Schematic and PCB - Finished traces and top and bottom ground plains - Added vias for copper islands / isolated copper - Generated pdf of schematic and pcb - Updated README 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
    [engemil_pmw3901mb.kicad_pcb, engemil_pmw3901mb.kicad_sch]
2025-06-12 - Added gerber files - Updated text on bottom silk layer - Updated images for readme file - Updated PCB PDF file
    [engemil_pmw3901mb-B_Cu.gbr, engemil_pmw3901mb-B_Mask.gbr, engemil_pmw3901mb-B_Paste.gbr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]
2025-06-23 Added 3 new components
    [bom.csv]
2025-06-24 - Removed 3v3 voltage regulator and two capacitors - Changed reference designators (C1,C2,...,U2,U3,...) - Added R4 - Marked C3 and C4 as not mount - Added comment about RC filter - Added pull-up res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
    [bom.csv, engemil_pmw3901mb.kicad_pcb, engemil_pmw3901mb.kicad_sch]
2025-06-24 - Finalized version 2 - Updated PCB pdf file - Updated README - Updated images - Updated PCB design - Updated gerber files
    [engemil_pmw3901mb-B_Cu.gbr, engemil_pmw3901mb-B_Mask.gbr, engemil_pmw3901mb-B_Paste.gbr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]
2025-06-25 Corrected BOM for version 2
    [bom.csv]
2025-06-26 Renamed gerbers zip file to include version in name
2025-06-26 - Updated Schematic date - Corrected schematic pdf file to match latest updates
    [engemil_pmw3901mb.kicad_sch]
2025-06-26 Corrected schematic pdf from portrait to landscape orientation

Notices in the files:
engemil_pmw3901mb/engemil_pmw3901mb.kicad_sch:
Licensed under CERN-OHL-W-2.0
